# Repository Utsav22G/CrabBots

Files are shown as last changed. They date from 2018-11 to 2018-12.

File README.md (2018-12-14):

# CrabBots
### Small robots that use colored light to interact with other robots and the environment to perform complex interactions. 

## Overview
To learn more about our project, visit our [website!](http://poe.olin.edu/2018/crabworks/)

This github serves a storage capsule for our CAD files, PCB designs, and code used in our project. 

## PCB (Robot)
Our PCB is based off the Arduino Uno and includes some additional features:
* An analog mux for an increased number of anlog input pins
* A dual h-bridge motor driver to power our motors
* A 3-axis accelerometer for tap/bump detection
* Support for an RGB strip. We used NeoPixels

Because our PCB follows the same avr architecture as the Arduino Uno (and uses the same Atmega328P-PB), any Arduino code can be
uploaded through the Arduino IDE compiler to program our boards. However, our boards are lacking usb-serial convertera so an external
usb-serial converter is needed ([this is what we used](https://www.sparkfun.com/products/9825)).

You might notice that our assembled PCBs are populated with only a fraction of the parts that are included in our layout. This is 
due to a radical change in our photodiode sensing circuit after shipping the boards to be manufactured. Fortunately, our new circuit
uses less parts so it's still easy to assemble a working board. 

If you are up for an extra challenge, feel free to submit a pull request for a flashy, new board.

## PCB (Beacon)
What is the best accessory for our CrabBot? A fancy flashlight that can be programmed to display any color and controlled with a
tactile toggle button, of course! Our beacons are a useful tool for debugging and controlling our bots.

The schematic for the board stayed mostly the same. An input for **gnd** and **vcc** are needed for the board to function. We also recommend adding a power switch so the Attiny 85 doesn't drain your battery over time.

## Software
Our final bots rely on two code files: chaser, chased. When uploaded to our CrabBots, this code will make them chase each other. The code is written in Arduino and relys on multiple libraries including the Adafruit sensor library. The appropriate packages that need to be downloaded can be found [here](https://learn.adafruit.com/adafruit-lis3dh-triple-axis-accelerometer-breakout/arduino) and [here](https://learn.adafruit.com/adafruit-neopixel-uberguide/basic-connections). 

## Mechanical Design
The final iteration of CAD can be found here. We printed the components on a Prusa with PLA filament. While this design should not
be constrained by the type of plastic or printer used, we can't guarantee success with another setup. 

## Assembly
While we currently don't have a thorough instruction set layed out, we recommend looking at all our pictures. You probably don't need
or want instructions anyways!

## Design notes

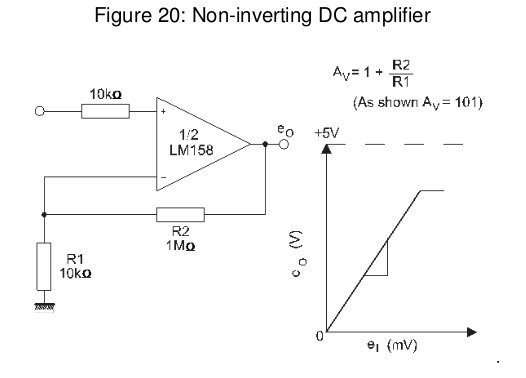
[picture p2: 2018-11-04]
res/lm358_schematic.png

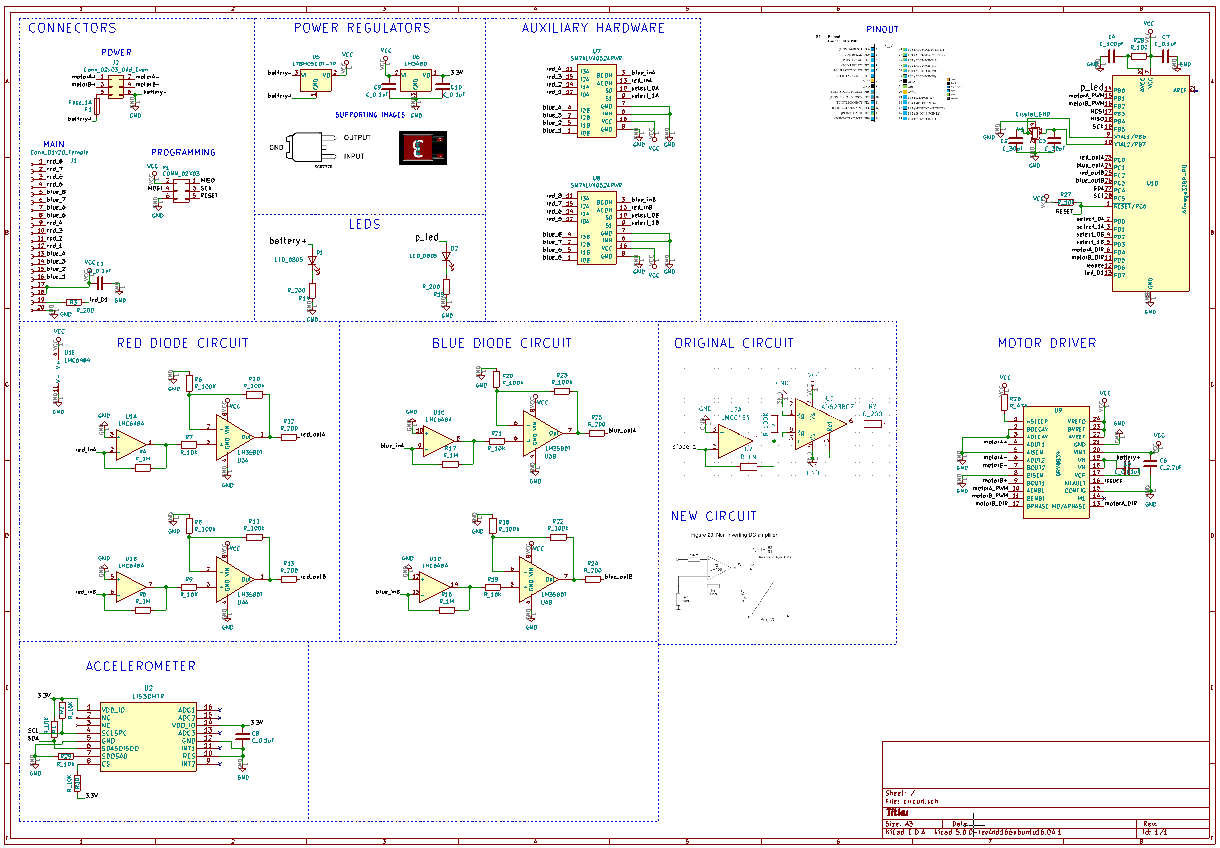
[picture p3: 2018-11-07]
res/circuit_schematic.png

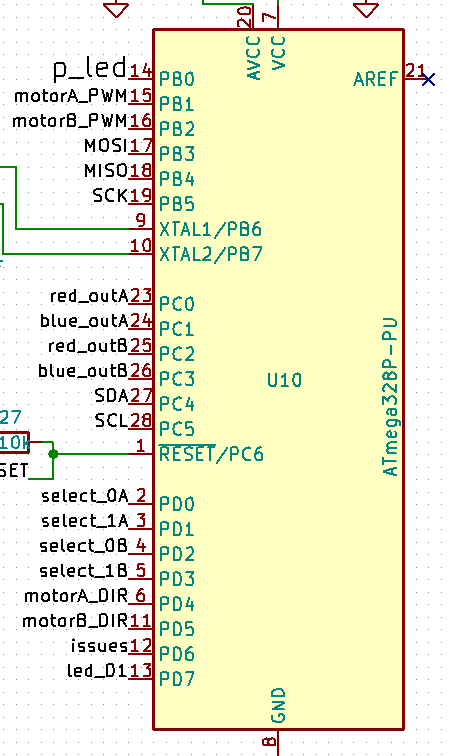
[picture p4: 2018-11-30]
res/atmega_pinout.png

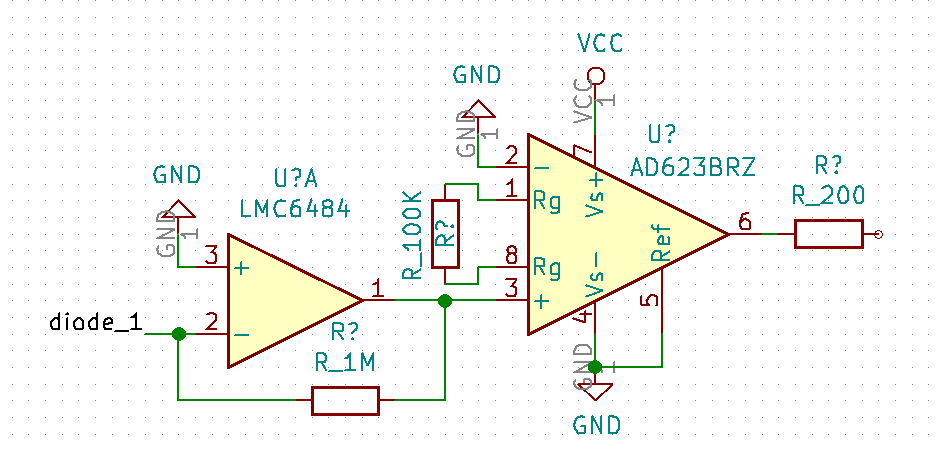
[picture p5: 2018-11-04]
res/original_schematic.png

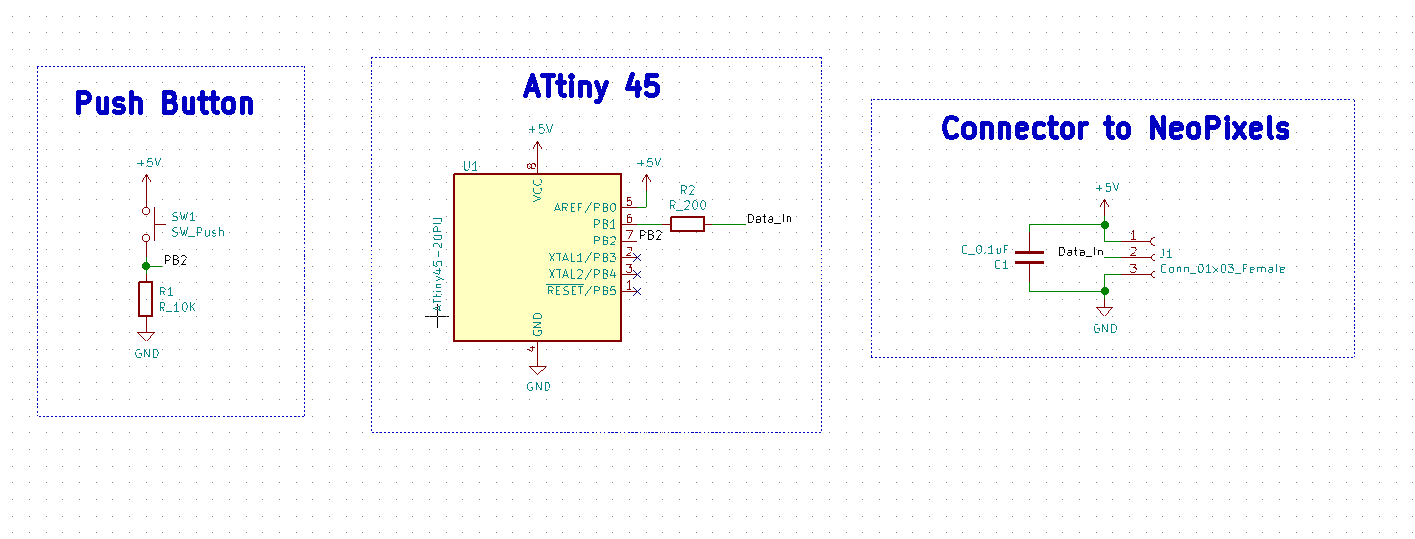
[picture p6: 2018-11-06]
beacon/Schematic.png

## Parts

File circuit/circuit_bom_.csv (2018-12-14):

Component | Description | Part | References | Value | Footprint | Quantity Per PCB | Datasheet | MPN | MFN | PurchasingLink | Package | Purchasing Link
1 | Capacitor, 0.1uF, 50V, 5%, 0805 | C_0.1uF | C5 | C_0.01uF | C_0805_OEM | 1 | http://datasheets.avx.com/X7RDielectric.pdf | 478-3352-1-ND | DK | https://www.digikey.com/product-detail/en/samsung-electro-mechanics/CL21B103KBCSFNC/1276-2439-1-ND/3890525
2 | Capacitor, 0.1uF, 50V, 5%, 0805 | C_0.1uF | C1 C7 C8 C9 C10 | C_0.1uF | C_0805_OEM | 5 | http://datasheets.avx.com/X7RDielectric.pdf | 478-3352-1-ND | DK Digi-Key | https://www.digikey.com/products/en?keywords=478-3352-1-ND | Value
3 | Capacitor, 100pF, 50V, 5%, 0805 | C_100pF | C4 | C_100pF | C_0805_OEM | 1 | https://content.kemet.com/datasheets/KEM_C1003_C0G_SMD.pdf | 399-1122-1-ND | Digi-Key | https://www.digikey.com/product-detail/en/kemet/C0805C101J5GACTU/399-1122-1-ND/411397 | Value
4 | Capacitor, 2.2uF, 10V, 10%, 0603 | C_2.2uF | C6 | C_2.2uF | R_0805_OEM | 1 | http://www.yageo.com/documents/recent/UPY-GPHC_X5R_4V-to-50V_25.pdf | 311-1451-1-ND | DK | https://www.digikey.com/product-detail/en/taiyo-yuden/EMK212BJ225KGHT/587-3323-1-ND/4157368
5 | Capacitor, 30pF, 50V, 5%, 0805 | C_30pF | C2 C3 | C_30pF | C_0805_OEM | 2 | https://media.digikey.com/pdf/Data%20Sheets/Samsung%20PDFs/CL_Series_MLCC_ds.pdf | 1276-1130-1-ND | DK | https://www.digikey.com/product-detail/en/samsung-electro-mechanics-america-inc/CL21C300JBANNNC/1276-1130-1-ND/3889216
6 | LED, Green, 2.2V, 20mA, 0805 | LED_0805 | D1 D2 | LED_0805 | LED_0805_OEM | 2 | http://www.osram-os.com/Graphics/XPic9/00078860_0.pdf | 475-1410-1-ND | DK | https://www.digikey.com/products/en?keywords=475-1410-1-ND
7 | Fuse | Fuse | F1 | Fuse_1A | R_0805_OEM | 1 | https://industrial.panasonic.com/cdbs/www-data/pdf/AFA0000/AFA0000C7.pdf
8 | Generic connector, single row, 01x20, script generated (kicad-library-utils/schlib/autogen/connector/) | Conn_01x20_Female | J1 | Conn_01x20_Female | Pin_Header_Straight_2x10 | 1 | ~
9 | Generic connector, double row, 02x03, odd/even pin numbering scheme (row 1 odd numbers, row 2 even numbers), script generated (kicad-library-utils/schlib/autogen/connector/) | Conn_02x03_Odd_Even | J2 | Conn_02x03_Odd_Even | Pin_Header_Straight_2x03 | 1 | ~
10 |  | CONN_02X03-formula | P1 | CONN_02X03 | Pin_Header_Straight_2x03 | 1 | http://portal.fciconnect.com/Comergent//fci/drawing/67996.pdf | 609-3234-ND | Digi-Key | https://www.digikey.com/product-detail/en/amphenol-fci/67997-206HLF/609-3234-ND/1878491 | Value
11 |  | R_100 | R28 | R_100 | R_0805_OEM | 1 | https://www.seielect.com/Catalog/SEI-rncp.pdf | RNCP0805FTD100RCT-ND | Digi-Key | https://www.digikey.com/products/en?keywords=RNCP0805FTD100RCT-ND | Value
12 |  | R_100K | R6 R8 R10 R11 R18 R20 R22 R23 | R_100K | R_0805_OEM | 8 | https://industrial.panasonic.com/cdbs/www-data/pdf/RDA0000/AOA0000C304.pdf | P100KCCT-ND | DK | https://www.digikey.com/product-detail/en/panasonic-electronic-components/ERJ-6ENF1003V/P100KCCT-ND/119551
13 |  | R_10K | R1 R2 R7 R9 R19 R21 R29 R30 | R_10K | R_0805_OEM | 8 | http://www.bourns.com/data/global/pdfs/CRS.pdf | CRS0805-FX-1002ELFCT-ND | DK | https://www.digikey.com/products/en?keywords=CRS0805-FX-1002ELFCT-ND
14 |  | R_10k-formula | R27 | R_10k | R_0805_OEM | 1 | http://www.bourns.com/data/global/pdfs/CRS.pdf | CRS0805-FX-1002ELFCT-ND | Digi-Key | https://www.digikey.com/products/en?keywords=CRS0805-FX-1002ELFCT-ND | Value
15 |  | R_1M | R4 R5 R16 R17 | R_1M | R_0805_OEM | 4 | https://www.seielect.com/Catalog/SEI-rncp.pdf | RMCF0805JT1M00CT-ND | DK | https://www.digikey.com/product-detail/en/stackpole-electronics-inc/RMCF0805JT1M00/RMCF0805JT1M00CT-ND/1942600
16 |  | R_200 | R3 R12 R13 R14 R15 R24 R25 | R_200 | R_0805_OEM | 7 | https://www.seielect.com/Catalog/SEI-RMCF_RMCP.pdf | RMCF0805JT200RCT-ND | DK | https://www.digikey.com/products/en?keywords=RMCF0805JT200RCT-ND
17 |  | R_1K | R26 | R_47K | R_0805_OEM | 1 | https://www.seielect.com/Catalog/SEI-rncp.pdf | RNCP0805FTD1K00CT-ND | DK | https://www.digikey.com/products/en?keywords=RNCP0805FTD1K00CT-ND
18 |  | ATmega328P-PU-MCU_Microchip_ATmega | U10 | ATmega328P-PU | ATMEGA_328PB_CONN | 1 | http://ww1.microchip.com/downloads/en/DeviceDoc/ATmega328_P%20AVR%20MCU%20with%20picoPower%20Technology%20Data%20Sheet%2040001984A.pdf
19 |  | DRV8834-formula | U9 | DRV8834 | DRV8834PWP | 1 | www.ti.com/lit/ds/symlink/drv8834.pdf |  |  |  |  | https://www.digikey.com/product-detail/en/texas-instruments/DRV8834PWP/296-30428-5-ND/3088200
20 | 1A Low Dropout regulator, positive, 5.0V fixed output, SOT-223 | AMS1117-5.0 | U5 | L78M05CDT-TR | L78M05CDT-TR | 1 | www.st.com/content/ccc/resource/technical/document/datasheet/d7/5f/dc/5c/d5/b6/48/7c/CD00000447.pdf/files/CD00000447.pdf/jcr:content/translations/en.CD0000044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
21 |  | LIS3DHTR-formula | U2 | LIS3DHTR | LIS3DHTR | 1
22 | Linear regulator, 30V max input, 3.3V output, 100mA | LM3480 | U6 | LM3480 | SOT-23 | 1 | http://www.ti.com/lit/ds/symlink/lm3480.pdf | LM3480IM3-3.3CT-ND | DK | https://www.digikey.com/product-detail/en/texas-instruments/LM3480IM3-3.3/LM3480IM3-3.3CT-ND/3701583
23 |  | LM358DT-formula | U3 U4 | LM358DT | SO-8_5.3x6.2mm_Pitch1.27mm | 2 | www.st.com/content/ccc/resource/technical/document/datasheet/61/46/87/01/98/ed/44/c5/CD00000464.pdf/files/CD00000464.pdf/jcr:content/translations/en.CD0000046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 |  |  | https://www.digikey.com/product-detail/en/stmicroelectronics/LM358DT/497-1591-1-ND/592083
24 | Quad CMOS Rail-to-Rail Input and Output Operational Amplifier, DIP-14/SOIC-14 | LMC6484 | U1 | LMC6484 | SOIC-14_3.9x8.7mm_Pitch1.27mm | 1 | http://www.ti.com/lit/ds/symlink/lmc6484.pdf
25 |  | SN74LV4052APWR-formula | U7 U8 | SN74LV4052APWR | TSSOP-16_4.4x5mm_Pitch0.65mm | 2 | www.ti.com/lit/ds/symlink/sn74lv4052a.pdf |  |  |  |  | https://www.digikey.com/product-detail/en/texas-instruments/SN74LV4052APWR/296-3831-1-ND/390425
26 | CRYSTAL 16.0000MHZ 18PF SMD | Crystal_SMD | Y1 | Crystal_SMD | Crystal_SMD_FA238 | 1 | http://www.txccorp.com/download/products/quartz_crystals/2015TXC_7M_17.pdf | 887-1125-1-ND | DK | https://www.digikey.com/product-detail/en/txc-corporation/7M-16.000MAAJ-T/887-1125-1-ND/2119014
Component Groups: | 26
Component Count: | 57
Fitted Components: | 57
Number of PCBs: | 1
Total components: | 57
Schematic Version:
Schematic Date:
BoM Date: | Wed 21 Nov 2018 11:47:25 PM EST
Schematic Source: | /home/utsav22g/Olin Stuff/CrabBots/circuit/circuit.sch
KiCad Version: | Eeschema 5.0.1-33cea8e~68~ubuntu18.04.1

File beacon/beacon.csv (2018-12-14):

Id | Designator | Package | Quantity | Designation | Supplier and ref
1 | C1 | C_0805_OEM | 1 | C_0.1uF
2 | J1 | Connector | 1 | Conn_01x03_Female
3 | R1 | R_0805_OEM | 1 | R_10K
4 | R2 | R_0805_OEM | 1 | R_200
5 | SW1 | push_button | 1 | SW_Push
6 | U1 | DIP-8_W7.62mm_Socket | 1 | ATtiny45-20PU

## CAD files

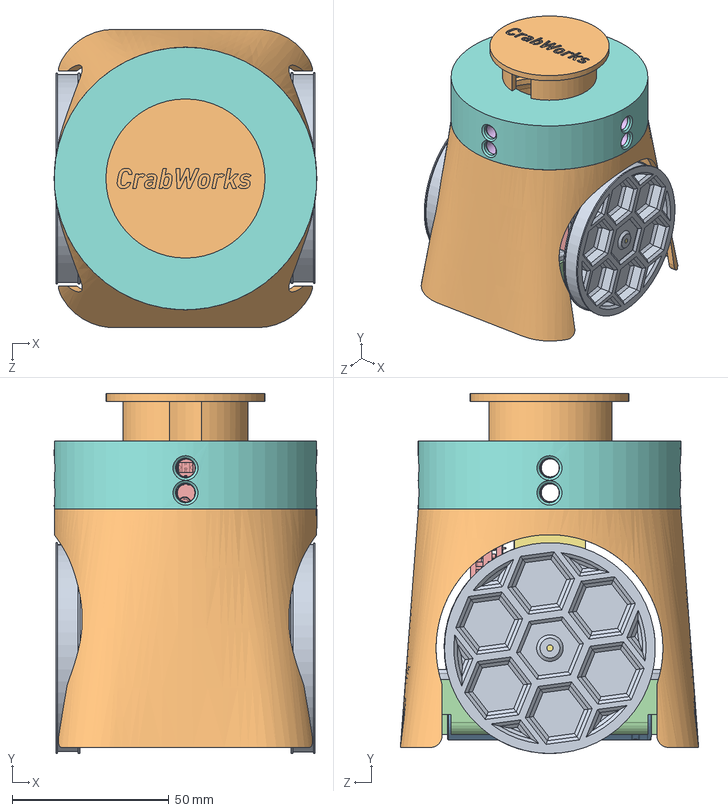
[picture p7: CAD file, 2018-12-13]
CrabBot_CAD/Assem_v5.SLDASM
83.8 x 114.9 x 95.2 mm
Chassis_v5
Shell_v5
2_cell_holder_18650_v5
arduino uno
DovetailLightSensor_v5 x 4
Pololu Mini Plastic Gearmotor x 2
Top_v5
wheel_v5 x 2
Beacon_Top_Bot_v5

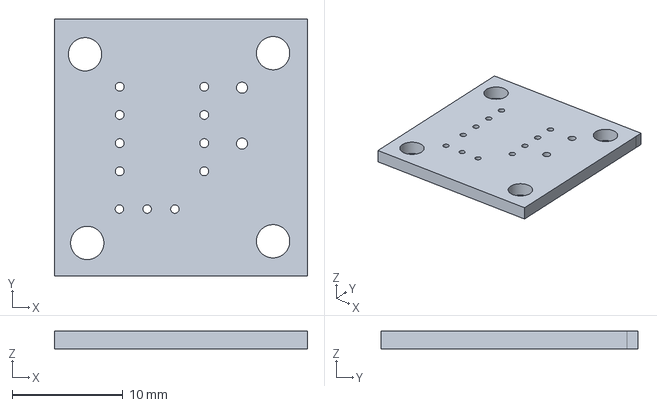
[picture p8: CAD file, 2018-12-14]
beacon/beacon.step
22.8 x 23.2 x 1.60 mm

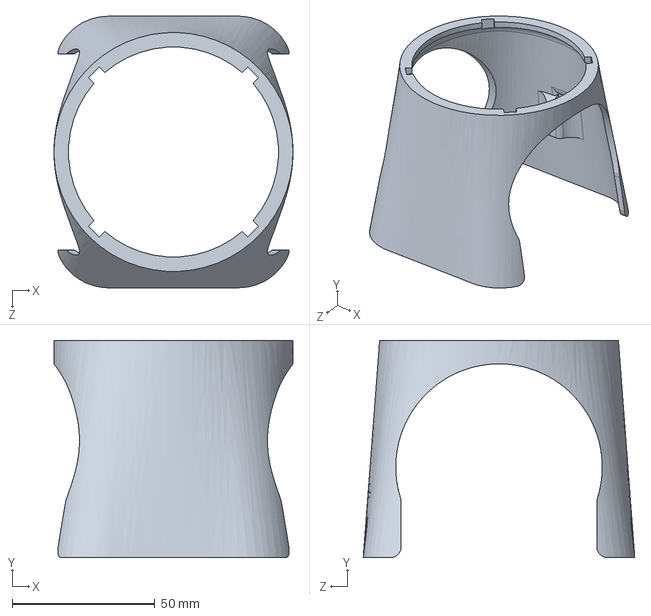
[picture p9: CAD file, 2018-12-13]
CrabBot_CAD/Shell_v5.SLDPRT
83.8 x 76.2 x 95.2 mm

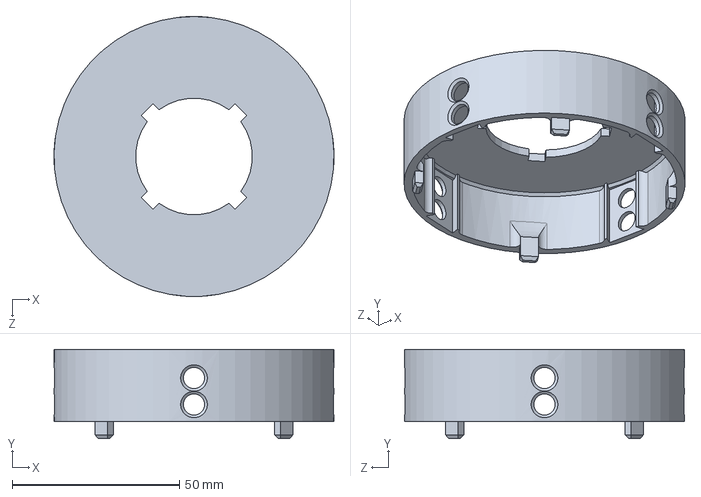
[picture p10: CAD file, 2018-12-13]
CrabBot_CAD/Top_v5.SLDPRT
83.8 x 26.7 x 83.8 mm

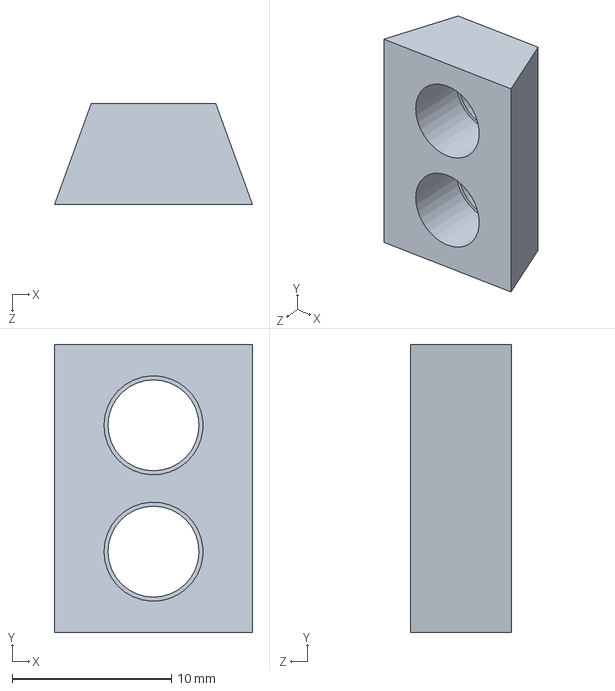
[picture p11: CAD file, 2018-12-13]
CrabBot_CAD/DovetailLightSensor_v5.SLDPRT
12.4 x 18.1 x 6.35 mm

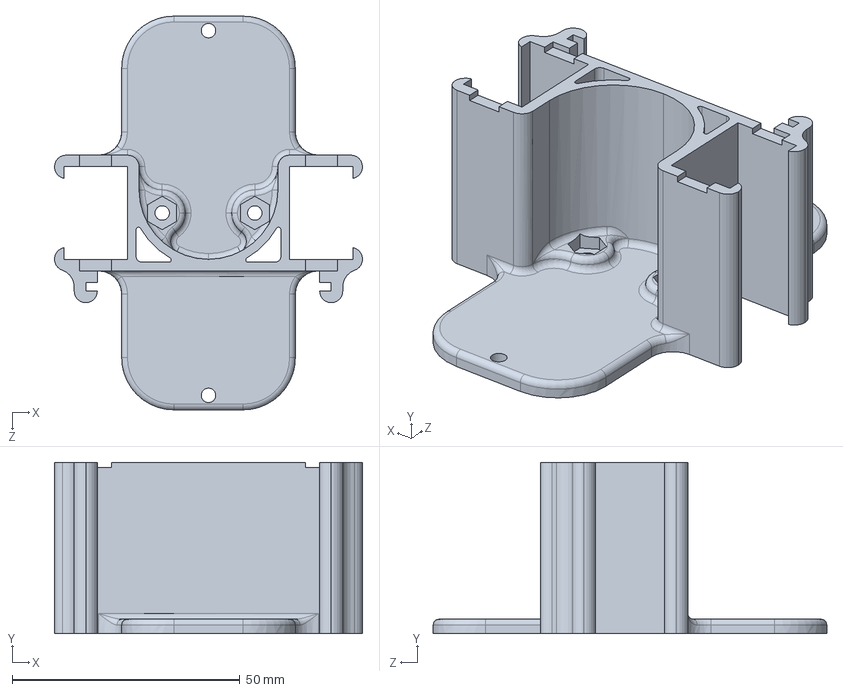
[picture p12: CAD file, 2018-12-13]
CrabBot_CAD/Chassis_v5.SLDPRT
67.6 x 37.6 x 86.4 mm

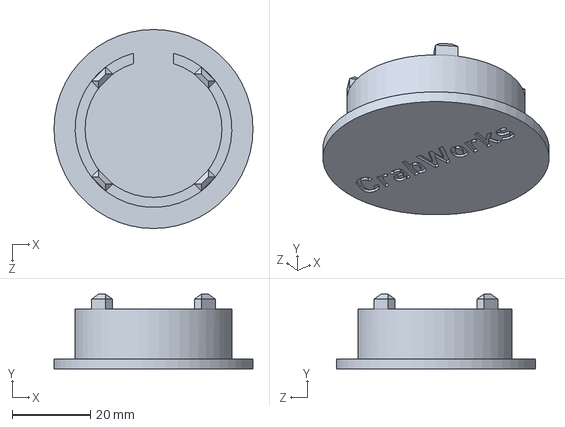
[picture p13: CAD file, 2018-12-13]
CrabBot_CAD/Beacon_Top_Bot_v5.SLDPRT
50.8 x 19.1 x 50.8 mm

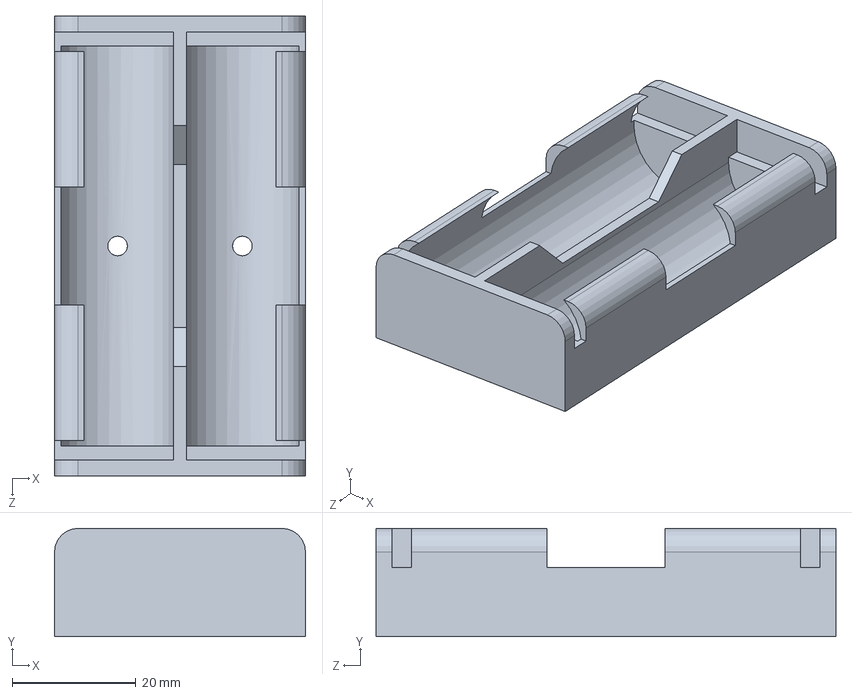
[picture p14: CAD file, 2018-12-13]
CrabBot_CAD/2_cell_holder_18650_v5.SLDPRT
40.6 x 17.5 x 74.4 mm

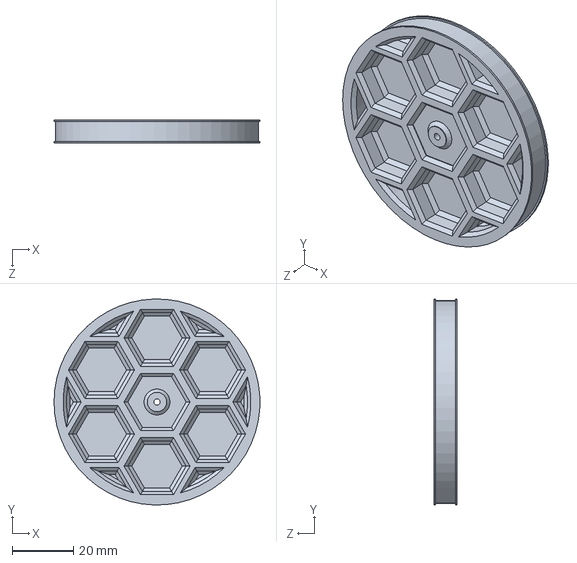
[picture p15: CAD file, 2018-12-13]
CrabBot_CAD/wheel_v5.SLDPRT
67.3 x 67.3 x 7.62 mm

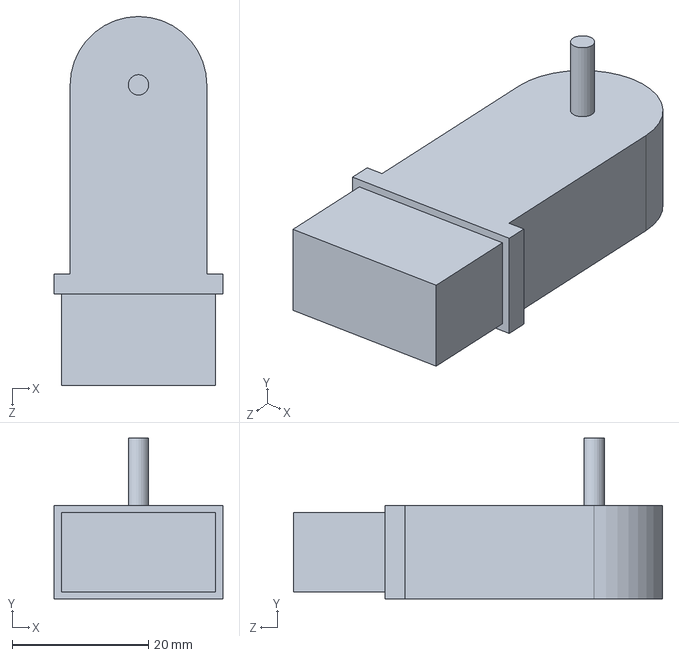
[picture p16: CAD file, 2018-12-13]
CrabBot_CAD/Pololu Mini Plastic Gearmotor.SLDPRT
24.7 x 23.6 x 54.1 mm

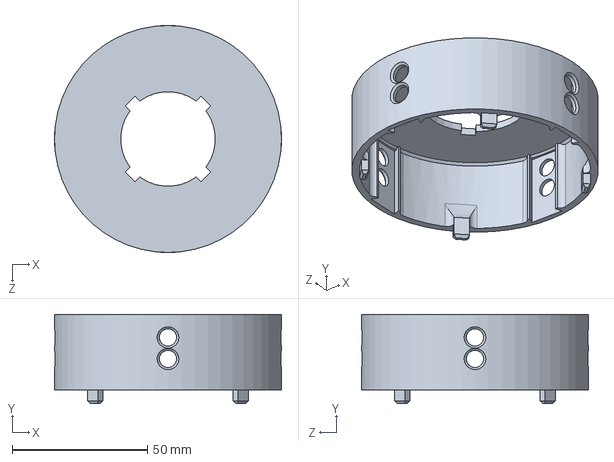
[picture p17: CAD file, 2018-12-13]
CrabBot_CAD/Top_v5_extended.SLDPRT
83.8 x 33.0 x 83.8 mm

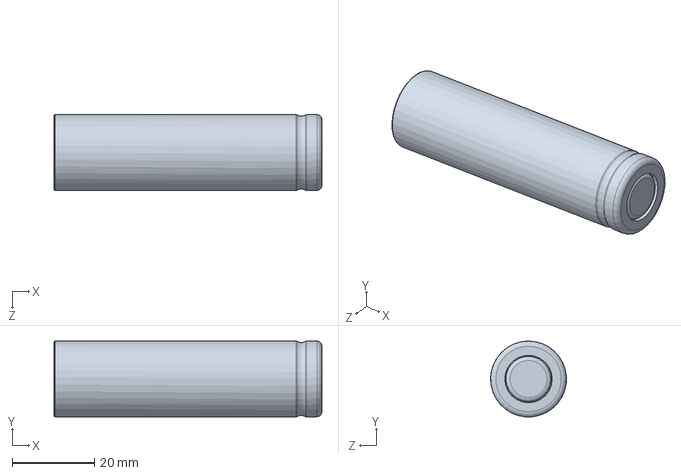
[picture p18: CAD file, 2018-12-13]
CrabBot_CAD/18650.SLDPRT
65.0 x 18.4 x 18.4 mm

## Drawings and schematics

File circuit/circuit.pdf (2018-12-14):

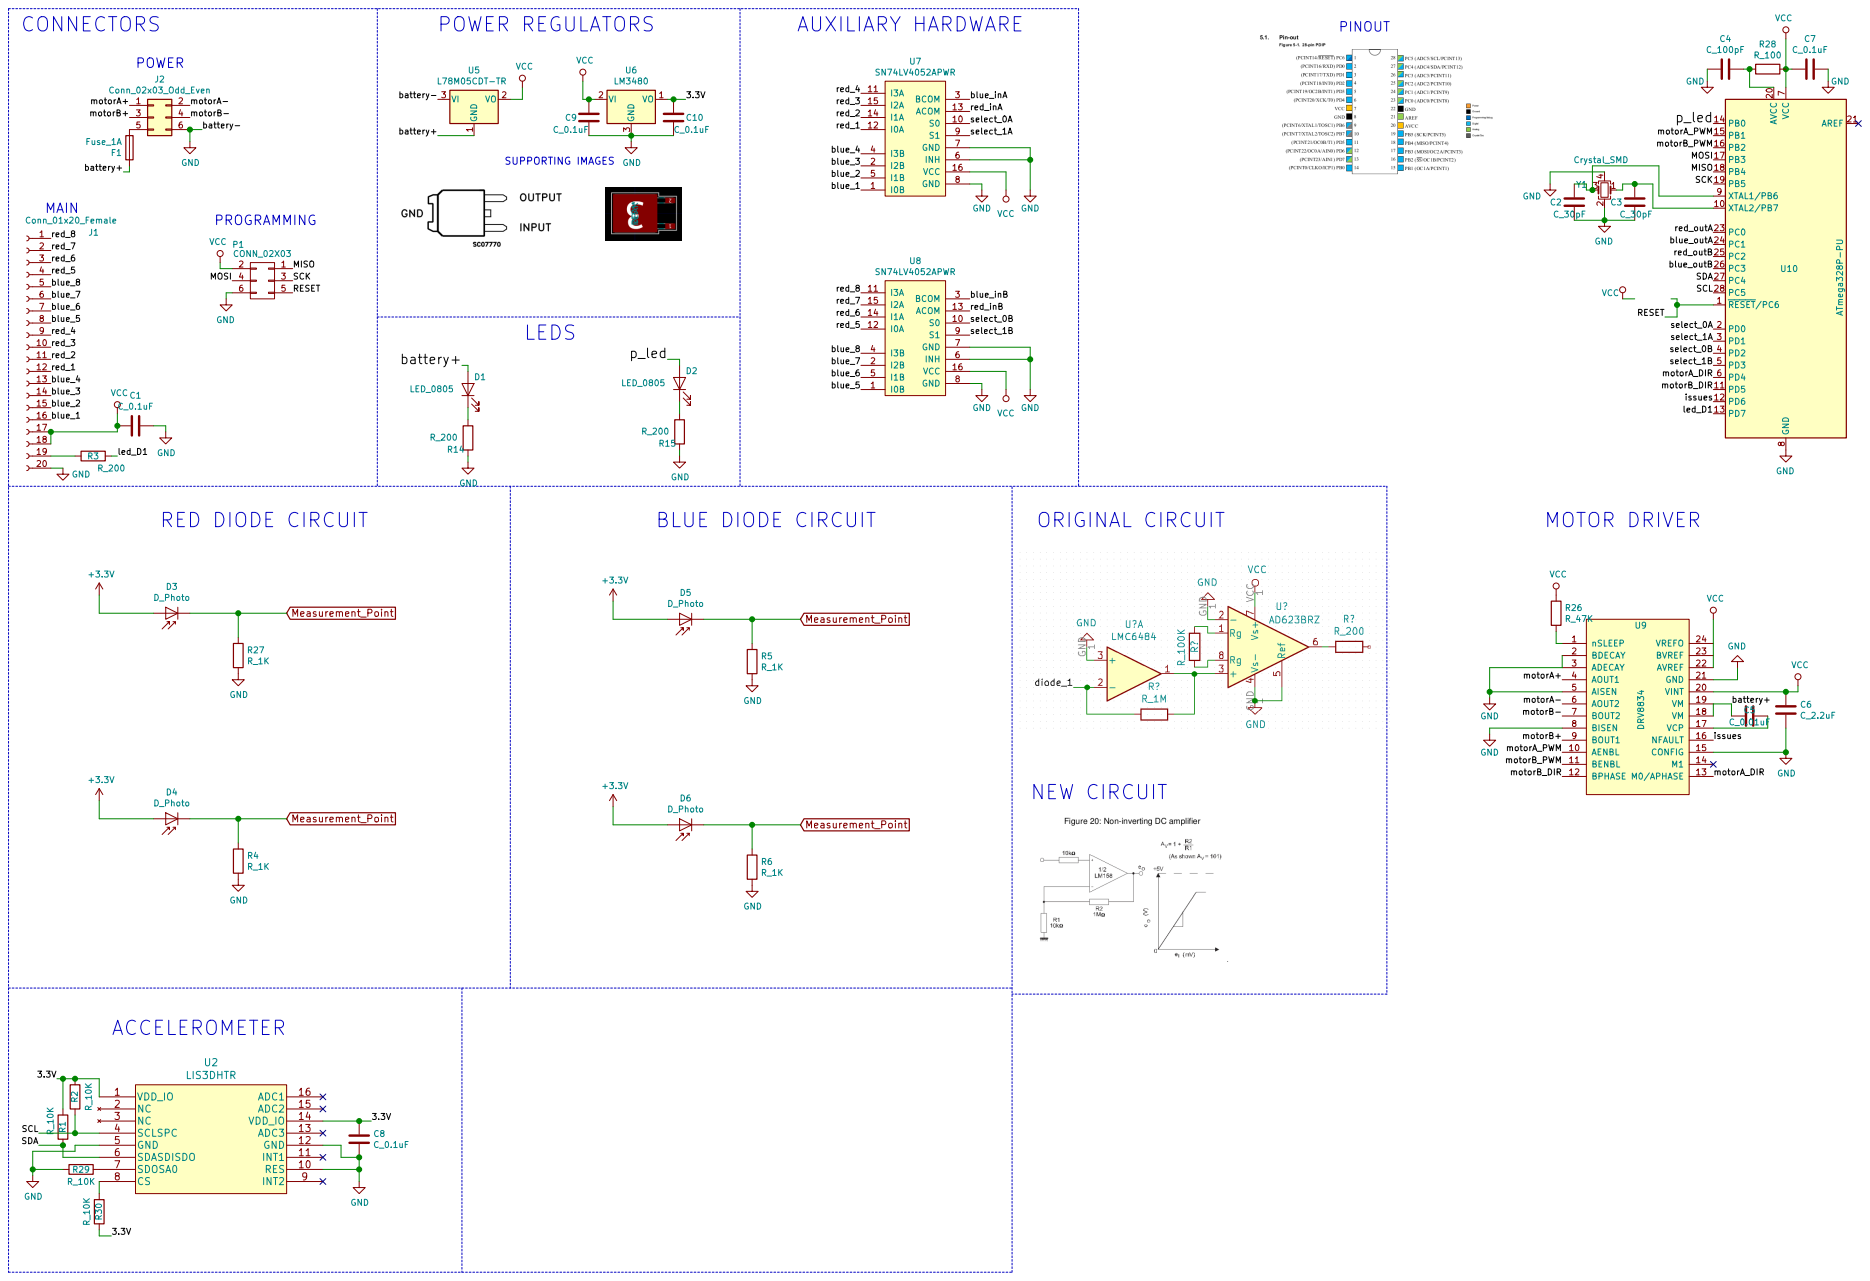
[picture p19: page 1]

LED_0805R15 R_200 GND SUPPORTING IMAGES LEDS

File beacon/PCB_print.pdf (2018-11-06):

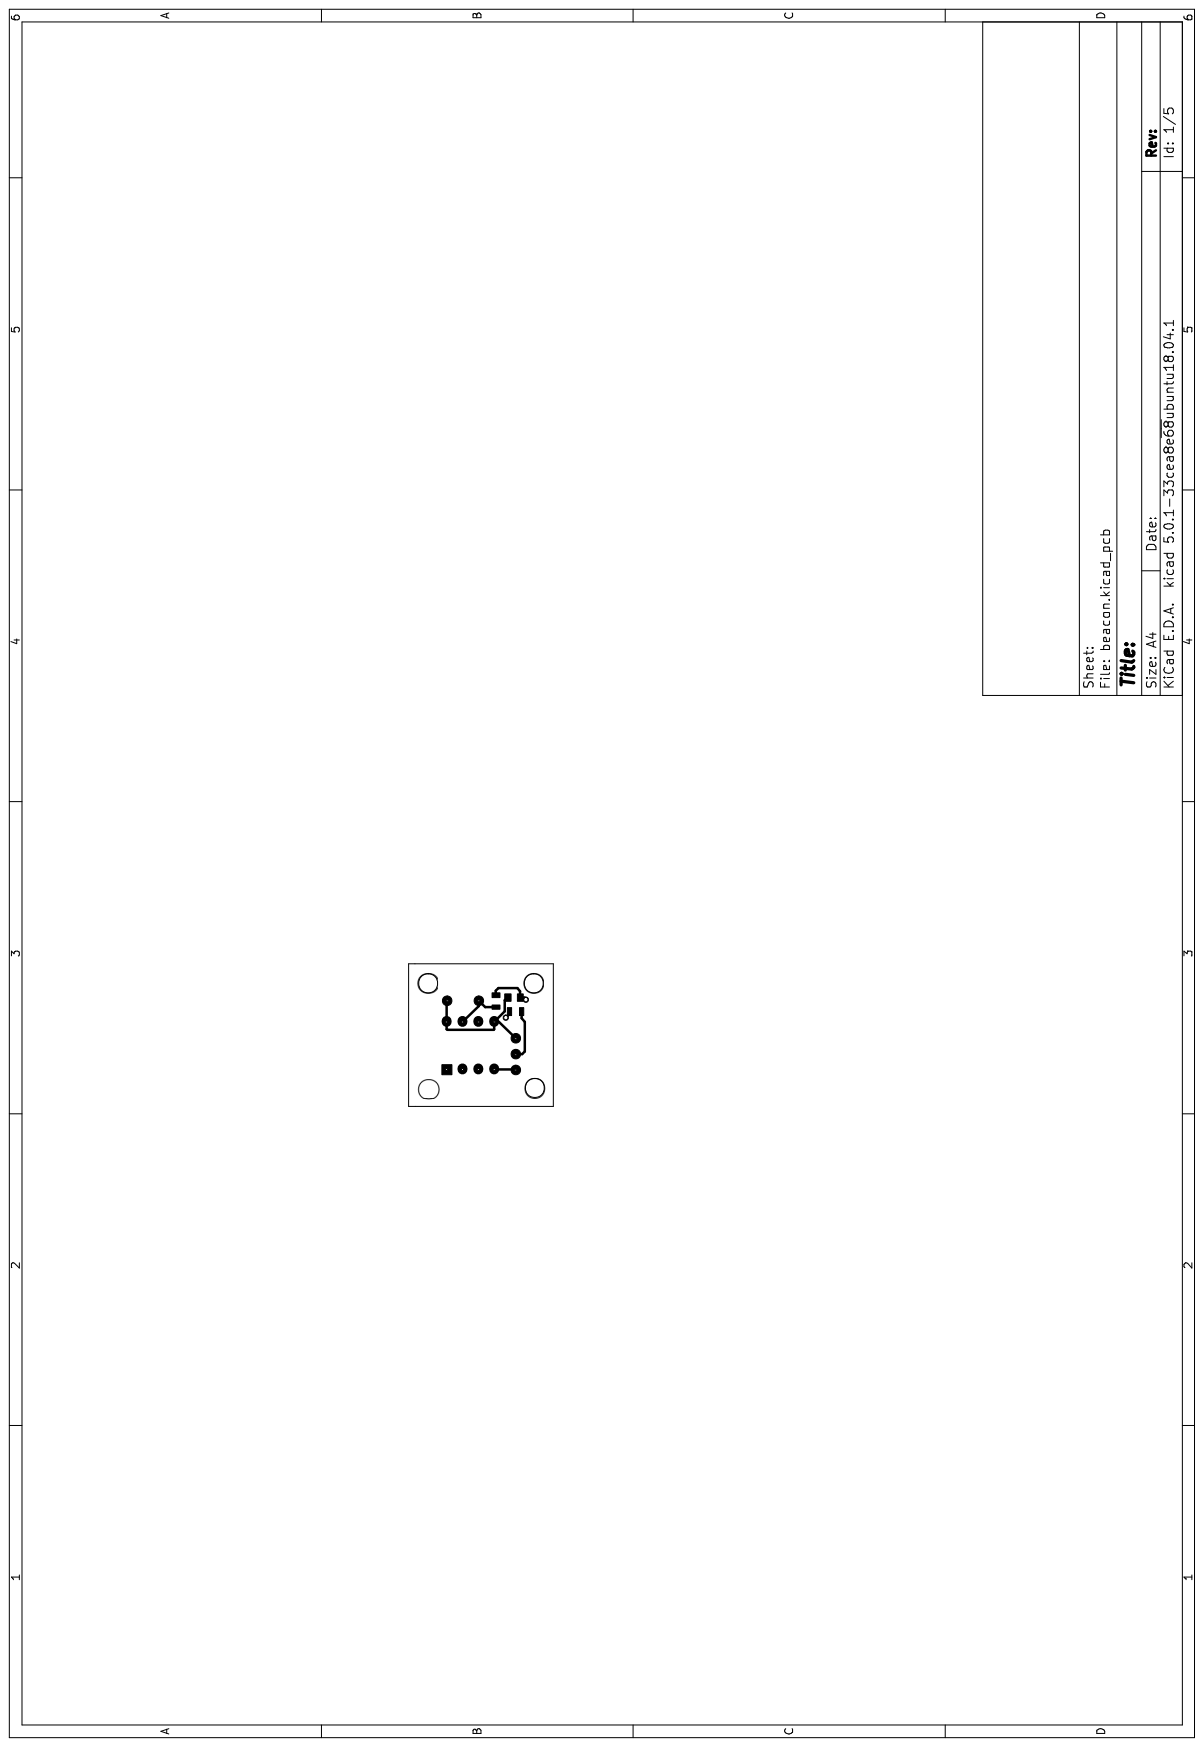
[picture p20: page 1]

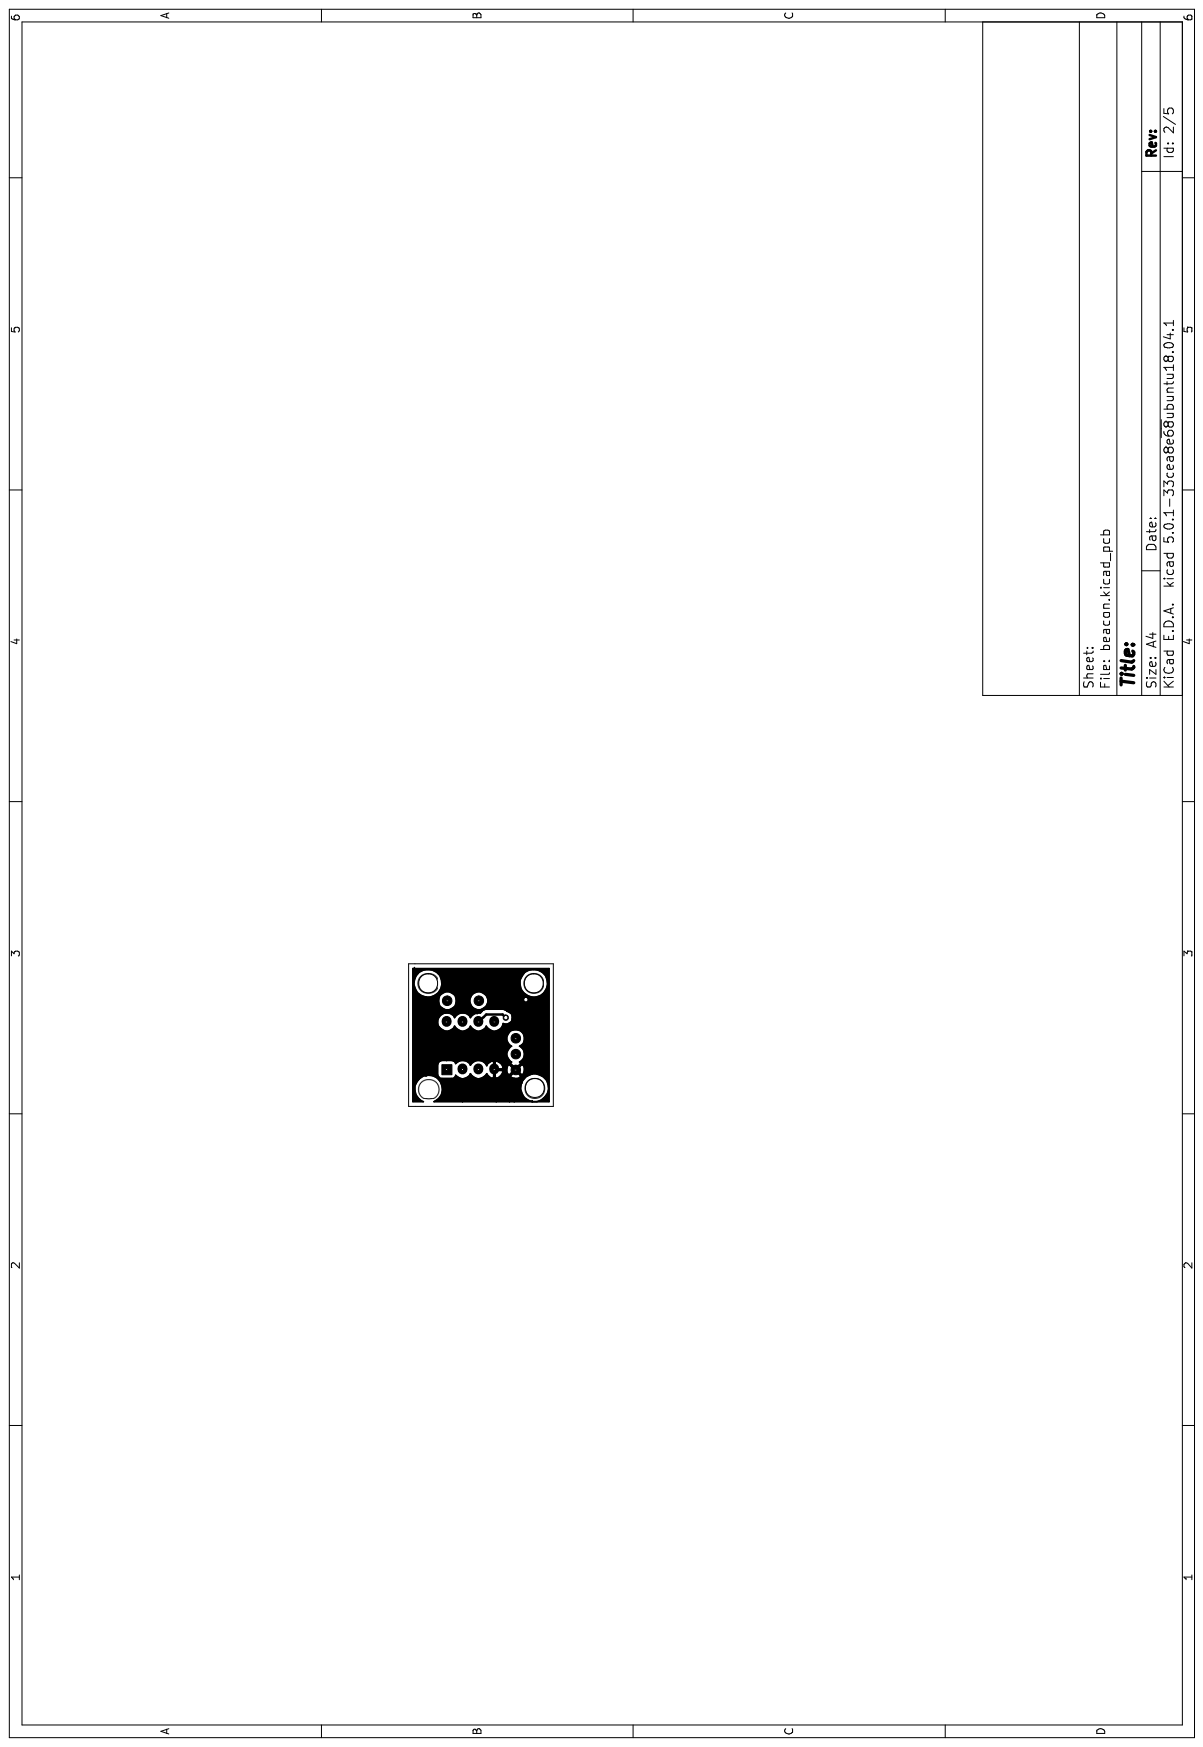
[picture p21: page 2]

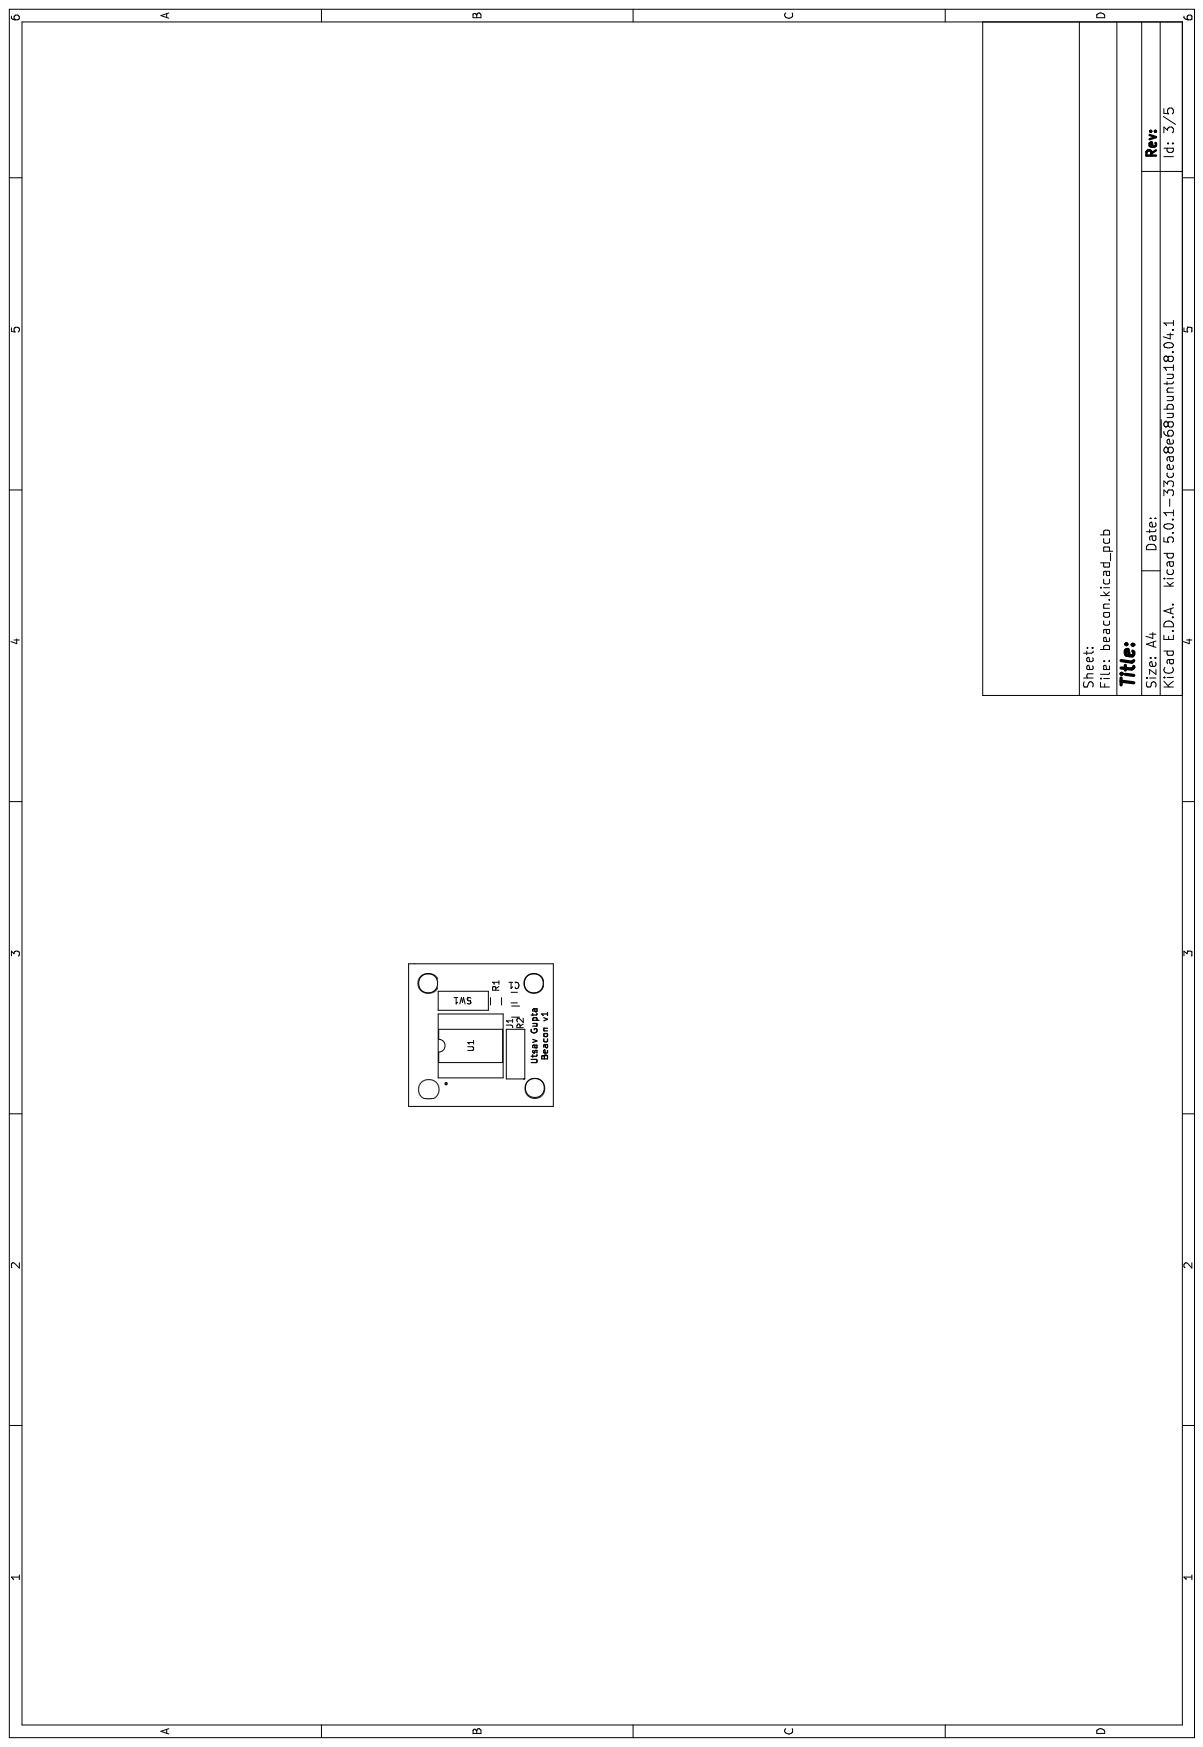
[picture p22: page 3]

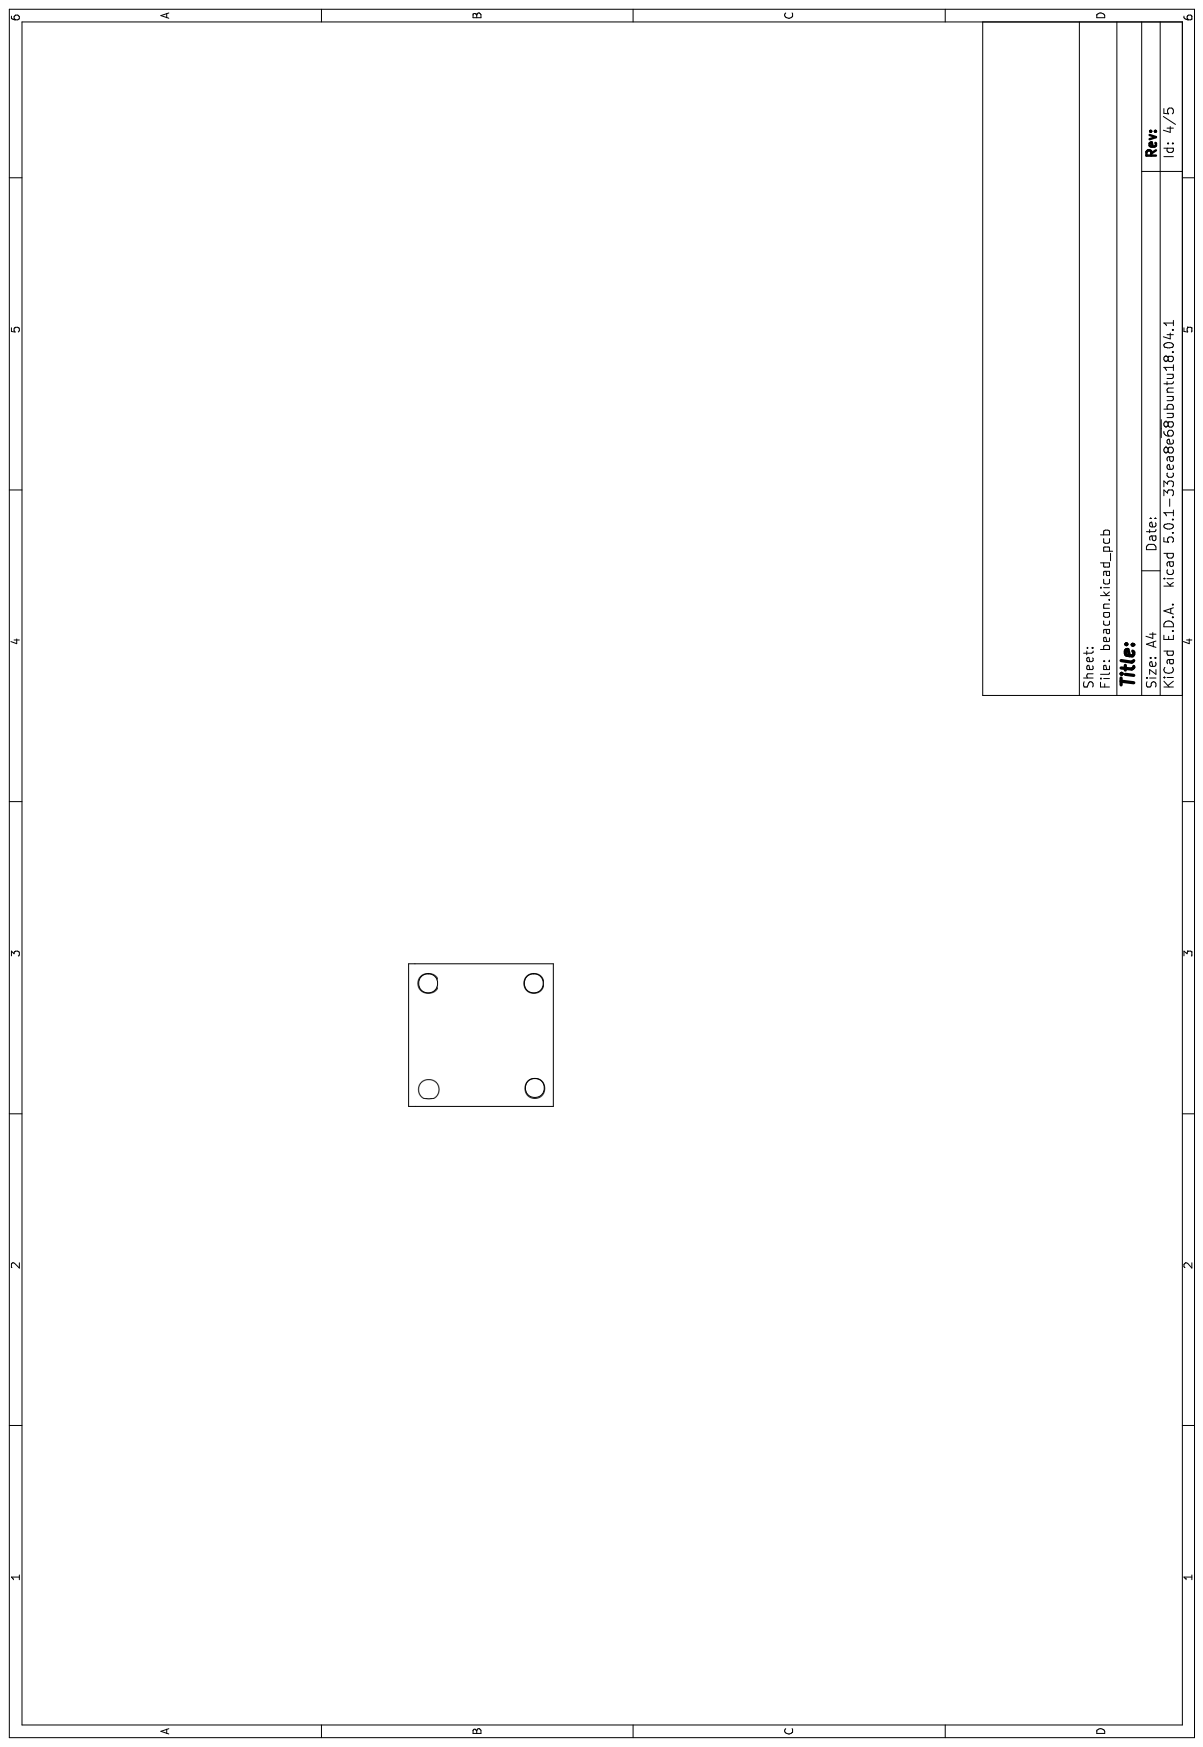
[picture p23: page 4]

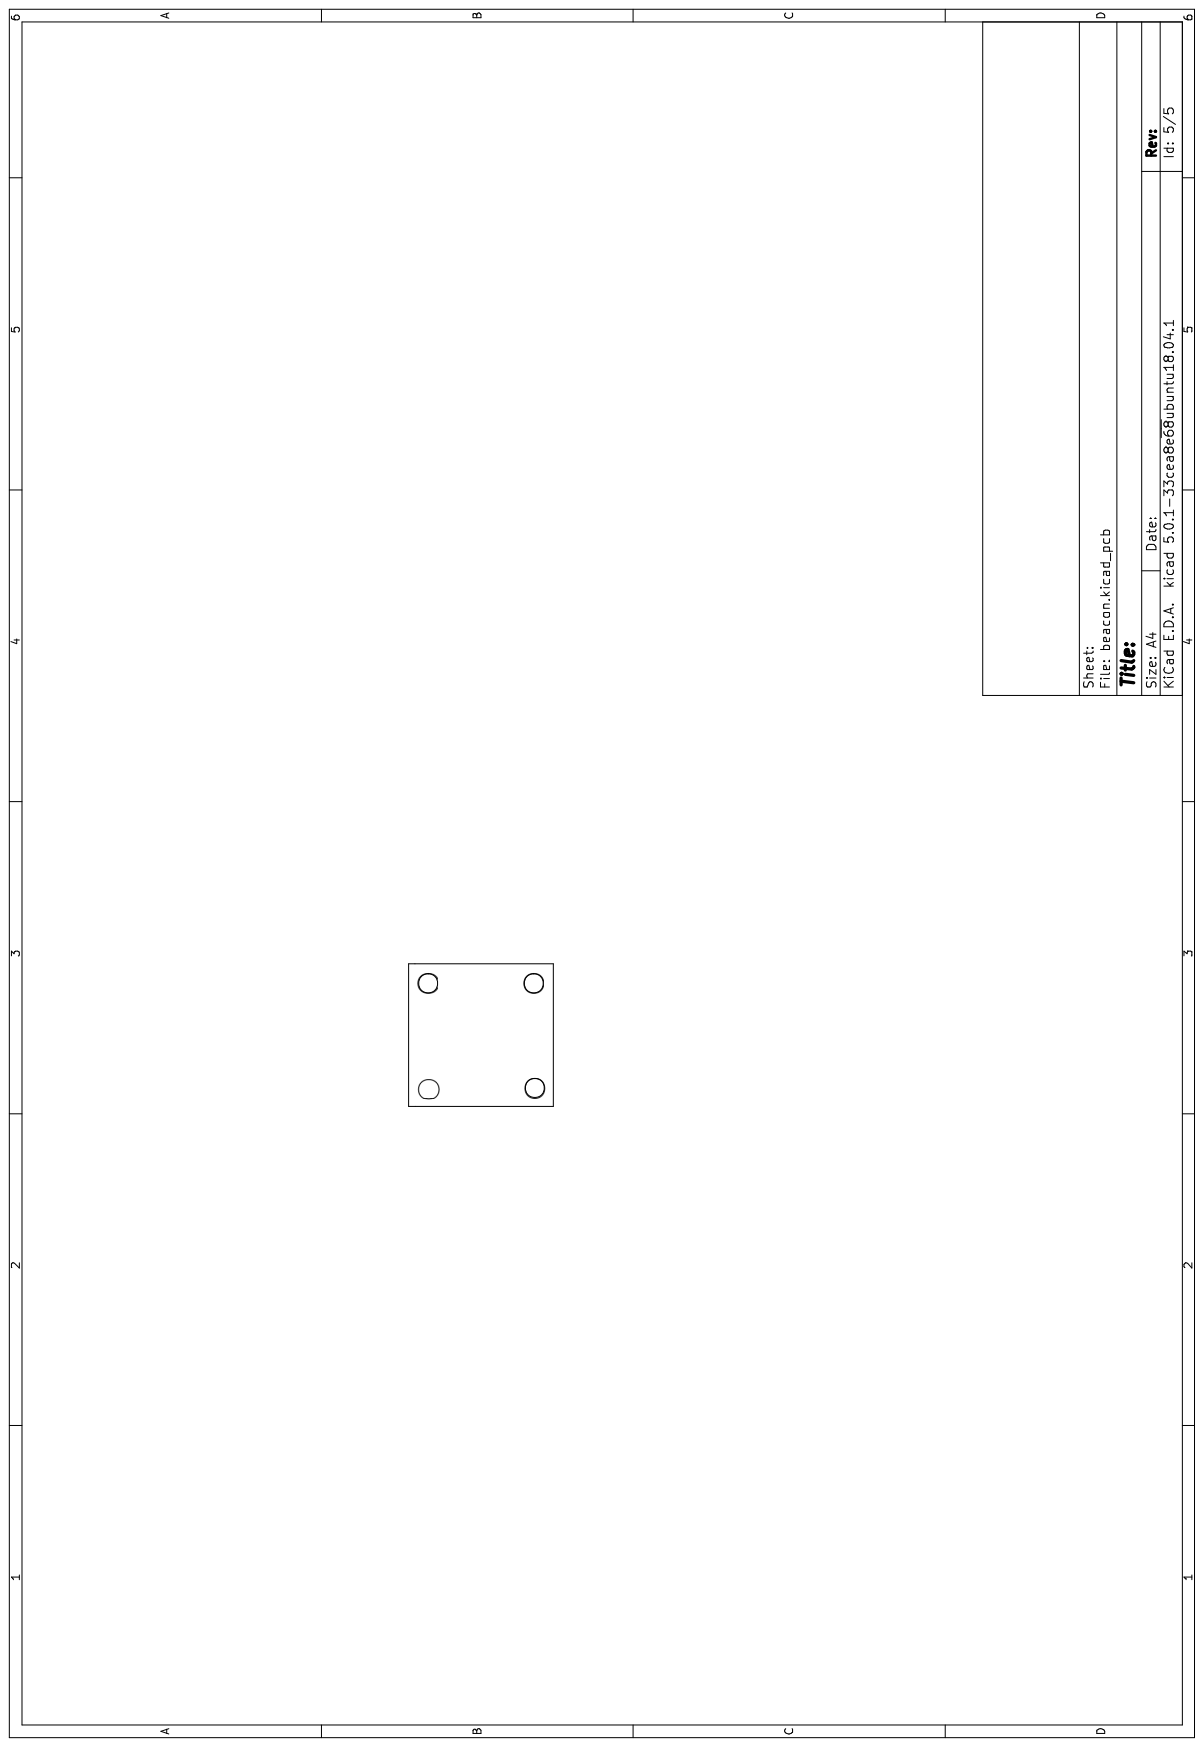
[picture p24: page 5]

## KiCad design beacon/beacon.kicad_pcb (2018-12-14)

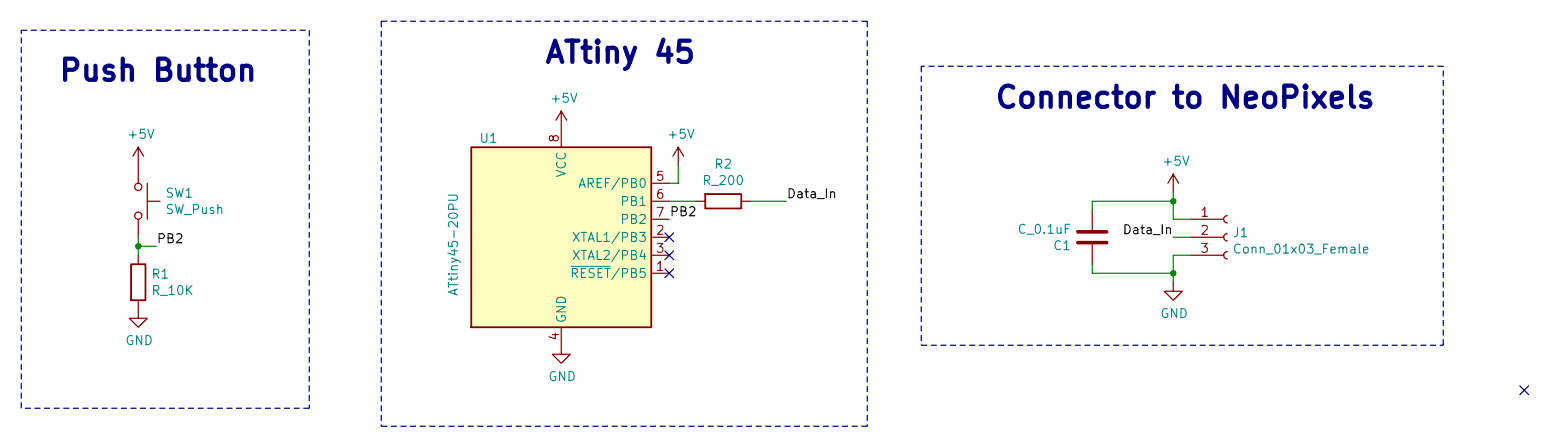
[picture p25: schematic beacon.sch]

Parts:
C1: C_0.1uF; C_0805_OEM; MPN 478-3352-1-ND
J1: Conn_01x03_Female; Connector
R1: R_10K; R_0805_OEM; MPN CRS0805-FX-1002ELFCT-ND
R2: R_200; R_0805_OEM; MPN RMCF0805JT200RCT-ND
SW1: SW_Push; push_button
U1: ATtiny45-20PU; DIP-8_W7.62mm_Socket

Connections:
+5V: C1.2, J1.1, SW1.1, U1.5 (AREF/PB0), U1.8 (VCC)
/Data_In: J1.2, R2.1
/PB2: R1.1, SW1.2, U1.7 (PB2)
GND: C1.1, J1.3, R1.2, U1.4 (GND)
unnamed: R2.2, U1.6 (PB1)

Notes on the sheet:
ATtiny 45
Connector to NeoPixels
Push Button

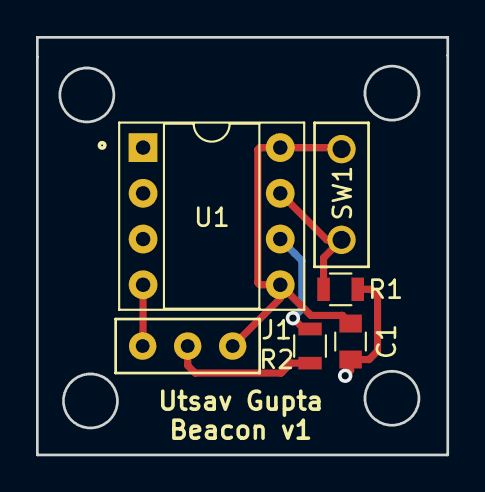
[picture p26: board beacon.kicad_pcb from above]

Board: 2 copper layers, 22.8 x 23.2 mm, 6 parts (0 on the bottom side), 5 nets.

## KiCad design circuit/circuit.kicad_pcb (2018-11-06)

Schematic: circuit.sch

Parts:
C1, C7, C8, C9, C10: C_0.1uF; C_0805_OEM; MPN 478-3352-1-ND
C2, C3: C_30pF; C_0805_OEM; MPN 1276-1130-1-ND
C4: C_100pF; C_0805_OEM; MPN 399-1122-1-ND
C5: C_0.01uF; C_0805_OEM; MPN 478-3352-1-ND
C6: C_2.2uF; R_0805_OEM; MPN 311-1451-1-ND
D1, D2: LED_0805; LED_0805_OEM; MPN 475-1410-1-ND
F1: Fuse_1A; R_0805_OEM
J1: Conn_01x20_Female; Pin_Header_Straight_2x10
J2: Conn_02x03_Odd_Even; Pin_Header_Straight_2x03
P1: CONN_02X03; Pin_Header_Straight_2x03; MPN 609-3234-ND
R1, R2, R7, R9, R19, R21, R29, R30: R_10K; R_0805_OEM; MPN CRS0805-FX-1002ELFCT-ND
R3, R12, R13, R14, R15, R24, R25: R_200; R_0805_OEM; MPN RMCF0805JT200RCT-ND
R4, R5, R16, R17: R_1M; R_0805_OEM; MPN RMCF0805JT1M00CT-ND
R6, R8, R10, R11, R18, R20, R22, R23: R_100K; R_0805_OEM; MPN P100KCCT-ND
R26: R_47K; R_0805_OEM; MPN RNCP0805FTD1K00CT-ND
R27: R_10k; R_0805_OEM; MPN CRS0805-FX-1002ELFCT-ND
R28: R_100; R_0805_OEM; MPN RNCP0805FTD100RCT-ND
U1: LMC6484; SOIC-14_3.9x8.7mm_Pitch1.27mm
U2: LIS3DHTR
U3, U4: LM358DT; SO-8_5.3x6.2mm_Pitch1.27mm
U5: L78M05CDT-TR
U6: LM3480; SOT-23; MPN LM3480IM3-3.3CT-ND
U7, U8: SN74LV4052APWR; TSSOP-16_4.4x5mm_Pitch0.65mm
U9: DRV8834; DRV8834PWP
U10: ATmega328P-PU; ATMEGA_328PB_CONN
Y1: Crystal_SMD; Crystal_SMD_FA238; MPN 887-1125-1-ND

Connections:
/3.3V: C8.1, C10.1, R1.2, R2.2, R30.1, U2.1, U2.14, U6.1
/MISO: P1.1, U10.18 (PB4)
/MOSI: P1.4, U10.17 (PB3)
/RESET: P1.5, R27.2, U10.1 (~RESET~/PC6)
/SCK: P1.3, U10.19 (PB5)
/SCL: R2.1, U2.4, U10.28 (PC5)
/SDA: R1.1, U2.6, U10.27 (PC4)
/battery+: C5.2, D1.2, F1.1, U5.1 (GND), U9.18, U9.19
/blue_1: J1.16, U7.1
/blue_2: J1.15, U7.5
/blue_3: J1.14, U7.2
/blue_4: J1.13, U7.4
/blue_5: J1.8, U8.1
/blue_6: J1.7, U8.5
/blue_7: J1.6, U8.2
/blue_8: J1.5, U8.4
/blue_inA: R17.2, U1.9 (-), U7.3
/blue_inB: R16.2, U1.13 (-), U8.3
/blue_outA: R25.1, U10.24 (PC1)
/blue_outB: R24.1, U10.26 (PC3)
/issues: U9.16, U10.12 (PD6)
/led_D1: R3.1, U10.13 (PD7)
/motorA+: J2.1, U9.4
/motorA-: J2.2, U9.6
/motorA_DIR: U9.13, U10.6 (PD4)
/motorA_PWM: U9.10, U10.15 (PB1)
/motorB+: J2.3, U9.9
/motorB-: J2.4, U9.7
/motorB_DIR: U9.12, U10.11 (PD5)
/motorB_PWM: U9.11, U10.16 (PB2)
/p_led: D2.2, U10.14 (PB0)
/red_1: J1.12, U7.12
/red_2: J1.11, U7.14
/red_3: J1.10, U7.15
/red_4: J1.9, U7.11
/red_5: J1.4, U8.12
/red_6: J1.3, U8.14
/red_7: J1.2, U8.15
/red_8: J1.1, U8.11
/red_inA: R4.2, U1.2 (-), U7.13
/red_inB: R5.2, U1.6 (-), U8.13
/red_outA: R12.1, U10.23 (PC0)
/red_outB: R13.1, U10.25 (PC2)
/select_0A: U7.10, U10.2 (PD0)
/select_0B: U8.10, U10.4 (PD2)
/select_1A: U7.9, U10.3 (PD1)
/select_1B: U8.9, U10.5 (PD3)
unnamed: C2.1, U10.9 (XTAL1/PB6), Y1.3
unnamed: C3.1, U10.10 (XTAL2/PB7), Y1.1
unnamed: C4.2, R28.1, U10.20 (AVCC)
unnamed: C5.1, U9.17
unnamed: D1.1, R14.2
unnamed: D2.1, R15.2
unnamed: F1.2, J2.5
unnamed: J1.19, R3.2
unnamed: R4.1, R7.2, U1.1
unnamed: R5.1, R9.2, U1.7
unnamed: R7.1, U3.3
unnamed: R9.1, U4.3
unnamed: R10.1, R12.2, U3.1
unnamed: R6.2, R10.2, U3.2
unnamed: R11.1, R13.2, U4.1
unnamed: R8.2, R11.2, U4.2
unnamed: R16.1, R19.2, U1.14
unnamed: R17.1, R21.2, U1.8
unnamed: R18.2, R22.2, U4.6
unnamed: R19.1, U4.5
unnamed: R20.2, R23.2, U3.6
unnamed: R21.1, U3.5
unnamed: R22.1, R24.2, U4.7
unnamed: R23.1, R25.2, U3.7
unnamed: R26.2, U9.1
unnamed: R29.1, U2.7
unnamed: R30.2, U2.8
VCC: C1.2, C6.1, C7.1, C9.1, J1.17, J1.18, P1.2, R26.1, R27.1, R28.2, U1.4 (V+), U3.8, U4.8, U5.2 (VO), U6.2, U7.16, U8.16, U9.20, U9.22, U9.23, U9.24, U10.7 (VCC)

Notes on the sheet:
RED DIODE CIRCUIT
BLUE DIODE CIRCUIT
ORIGINAL CIRCUIT
NEW CIRCUIT
CONNECTORS
MOTOR DRIVER
POWER REGULATORS
MAIN
PROGRAMMING
POWER
AUXILIARY HARDWARE
PINOUT
SUPPORTING IMAGES
LEDS
ACCELEROMETER

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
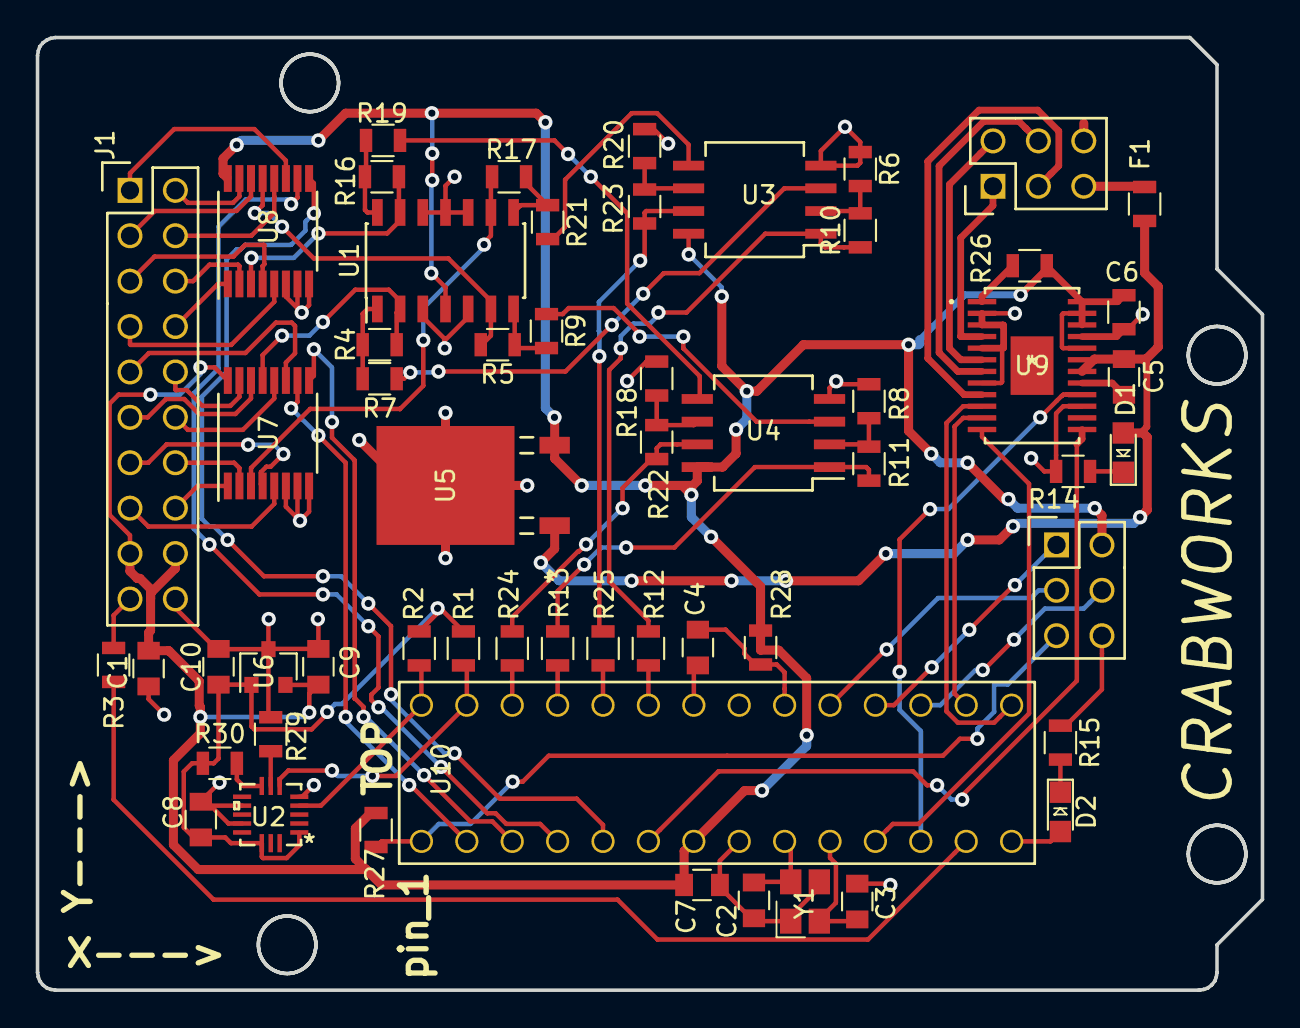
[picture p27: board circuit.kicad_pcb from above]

Board: 2 copper layers, 68.5 x 53.3 mm, 57 parts (0 on the bottom side), 76 nets.

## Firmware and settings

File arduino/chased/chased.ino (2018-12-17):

#include <Adafruit_NeoPixel.h>
#include <Wire.h>
#include <Adafruit_LIS3DH.h>
#include <Adafruit_Sensor.h>
#include "WS2812_Definitions.h"

// -----------------------
// DEFINE PINS
// -----------------------
#define RED A2 // input for red photodiode
#define BLUE A3 // input for blue photodiode

#define BPWM 10
#define APWM 9
#define BDIR 5
#define ADIR 4

#define MUX0 2
#define MUX1 3

#define LED_COUNT 20
#define LED_INPUT 7


// ---------------------
// DEFINE VARIABLES TO 
// READ SENSORS
// ---------------------

// front = 0, right = 1, left = 2, back = 3 
int init_red_front; // ambient reference value
int init_red_right;
int init_red_left;
int init_red_back;
int init_blue_front;
int init_blue_right;
int init_blue_left;
int init_blue_back;

int curr_red_front; // current value 
int curr_red_right;
int curr_red_left;
int curr_red_back;
int curr_blue_front;
int curr_blue_right;
int curr_blue_left;
int curr_blue_back;

int diff_red_front; // difference between ambient and current value
int diff_red_right;
int diff_red_left;
int diff_red_back;
int diff_blue_front;
int diff_blue_right;
int diff_blue_left;
int diff_blue_back;

int left2red;
int right2red;
int left2blue;
int right2blue;

int left3red;
int right3red;
int left3blue;
int right3blue;

int mux_delay = 5;
int motor_delay = 5;

unsigned long prevTime = 0;
unsigned long currTime;
int programCounter = 0;

bool bump = false;

// ---------------------
// DEFINE VARIABLES TO 
// SEND MOTOR COMMANDS
// ---------------------
float left1; // left motor commands to be summed 
float left2;
float left3;
float left4;

float right1; // right motor commands to be summed
float right2;
float right3;
float right4;

float left_total = 0;
float right_total = 0;

float sens = 2;
float scale = 1;
int bluesum;

// ---------------------
// DEFINE VARIABLES FOR
// LED STRIP
// ---------------------

int brightness = 64;
int R = 20;
int G = 0;
int B = 0;
Adafruit_NeoPixel strip = Adafruit_NeoPixel(LED_COUNT, LED_INPUT, NEO_RGB + NEO_KHZ800);

Adafruit_LIS3DH lis = Adafruit_LIS3DH();

void setup() {
  delay(5000);
  Serial.begin(9600);
  
  pinMode(RED,INPUT);
  pinMode(BLUE,INPUT);

  pinMode(APWM,OUTPUT);
  pinMode(ADIR,OUTPUT);

  pinMode(BPWM,OUTPUT);
  pinMode(BDIR,OUTPUT);
 
  pinMode(MUX0, OUTPUT);
  pinMode(MUX1, OUTPUT);

  pinMode(LED_INPUT, OUTPUT);

  digitalWrite(MUX0, HIGH); // set mux select to 0
  digitalWrite(MUX1, HIGH);
  delay(150);
  init_red_front = analogRead(RED); // take initial front values to calibrate
  init_blue_front = analogRead(BLUE);

  digitalWrite(MUX0, HIGH); // set mux select to 1
  digitalWrite(MUX1, LOW);
  delay(150);
  init_red_right = analogRead(RED); // take initial right values to calibrate
  init_blue_right = analogRead(BLUE);

  digitalWrite(MUX0, LOW); // set mux select to 2
  digitalWrite(MUX1, HIGH);
  delay(150);
  init_red_left = analogRead(RED); // take initial left values to calibrate
  init_blue_left = analogRead(BLUE);

  digitalWrite(MUX0, LOW); // set mux select to 3
  digitalWrite(MUX1, LOW);
  delay(150);
  init_red_back = analogRead(RED); // take initial back values to calibrate
  init_blue_back = analogRead(BLUE);

  if (! lis.begin(0x18)) {   // change this to 0x19 for alternative i2c address
    while (1){
      digitalWrite(8,HIGH);
      delay(250);
      digitalWrite(8,LOW);
      delay(250);
    }
  }
  lis.setRange(LIS3DH_RANGE_16_G);   // 2, 4, 8 or 16 G!

  strip.begin(); 
  colorWipe(strip.Color(0, 0, 0)); // Off   
  strip.show(); 
}

void loop() {
  
  currTime = millis();
  
  //ReadPhotodiodes();
  lis.read();      // get X Y and Z data at once
  sensors_event_t event; 
  lis.getEvent(&event);

  bluesum = diff_blue_front + diff_blue_right + diff_blue_left + diff_blue_back;
  if(abs(event.acceleration.z) > 10) {
    if (bump){
      bump = false;
    }
    else if(!bump && bluesum >= 7) {
      bump = true;
    }
  }

  if(bump) {
    colorWipe(strip.Color(0, 0, 0)); // Off
    analogWrite(APWM,0);
    analogWrite(BPWM,0);
    
  } else {
    colorWipe(strip.Color(0, 255, 0)); // Red
    ReadPhotodiodes();
    Move();

  }

  //Move();
}


int ReadPhotodiodes() {
  // ---------------------------
//  find current values of red
//  and blue by subtracting from
//  ambient value
//
//  take reading from front
//  r -> +L +R
//  b -> 0
//  scale values based on brightness 
// ----------------------------
   
  digitalWrite(MUX0, HIGH); // set mux select to 0
  digitalWrite(MUX1, HIGH);
  delay(mux_delay);
  //curr_red_front = analogRead(RED);
  curr_blue_front = analogRead(BLUE);

  //diff_red_front = curr_red_front - init_red_front;
  diff_blue_front = curr_blue_front - init_blue_front; // act based on difference from ambient value

  // left1 = sens*diff_red_front; // scaled motor values from front sensors
  // right1 = sens*diff_red_front;

  /*if(diff_red_front >= 10) {
    left1 = 100;
    right1 = 100;
  } else {
    left1 = 0;
    right1 = 0;
  }*/

// ---------------------------
//  take reading from right
//  r -> +L -R
//  b -> -L +R
// ----------------------------

  digitalWrite(MUX0, HIGH); // set mux select to 1
  digitalWrite(MUX1, LOW);
  delay(mux_delay);
  curr_red_right = analogRead(RED);
  curr_blue_right = analogRead(BLUE);

  diff_red_right = curr_red_right - init_red_right;
  diff_blue_right = curr_blue_right - init_blue_right;

  if(diff_red_right >= 5) {
    left2red = 10 + (sens*diff_red_right);
    right2red = 10 + (sens*diff_red_right);
  } else {
    left2red = 0;
    right2red = 0;
  }

  if(diff_blue_right >= 5) {
    left2blue = 50 + (sens*diff_blue_right);
    right2blue = 50 + (sens*diff_blue_right);
  } else {
    left2blue = 0;
    right2blue = 0;
  }

  left2 =  left2red -
  left2blue;
  //left2 = -left2blue;
  right2 = -right2red + right2blue;
  //right2 = right2blue;

  // left2 = (sens*diff_red_right) - (sens*diff_blue_right);
  // right2 = -(sens*diff_red_right) + (sens*diff_blue_right);

// ---------------------------
//  take reading from left
//  r -> -L +R
//  b -> +L -R
// ----------------------------

  digitalWrite(MUX0, LOW); // set mux select to 2
  digitalWrite(MUX1, HIGH);
  delay(mux_delay);
  curr_red_left = analogRead(RED);
  curr_blue_left = analogRead(BLUE);

  diff_red_left = curr_red_left - init_red_left;
  diff_blue_left = curr_blue_left - init_blue_left;

  if(diff_red_left >= 5) {
    left3red = 10 + (sens*diff_red_left);
    right3red = 10 + (sens*diff_red_left);
  } else {
    left3red = 0;
    right3red = 0;
  }

  if(diff_blue_left >= 5) {
    left3blue = 50 + (sens*diff_blue_left);
    right3blue = 50 + (sens*diff_blue_left);
  } else {
    left3blue = 0;
    right3blue = 0;
  }

  left3 = -left3red + left3blue;
  //left3 = left3blue;
  right3 = right3red - right3blue;
  //right3 = -right3blue;

  // ---------------------------
//  take reading from back
//  r -> 0
//  b -> +L +R
// ----------------------------

  digitalWrite(MUX0, LOW); // set mux select to 3
  digitalWrite(MUX1, LOW);
  delay(mux_delay);
  //curr_red_back = analogRead(RED);
  curr_blue_back = analogRead(BLUE);
  right_total = scale*(right1 + right2 + right3 + right4);

  //diff_red_back = curr_red_back - init_red_back;
  diff_blue_back = curr_blue_back - init_blue_back;

  // left4 = (sens*diff_red_back) + (sens*diff_blue_back);
  // right4 = 0;

  if(diff_blue_back >= 10) {
    left1 = 100;
    right1 = 100;
  } else {
    left1 = 0;
    right1 = 0;
  }
}

int Move() {
  // ----------------------------
  // Sum all motor response and 
  // send response to the motors
  // ----------------------------

   left_total = scale*(left1 + left2 + left3 + left4) - 40;
   right_total = scale*(right1 + right2 + right3 + right4) - 40;

   digitalWrite(ADIR,HIGH);
   digitalWrite(BDIR,LOW);

   /*if(diff_red_front >= 80) {
    left_total = 0;
    right_total = 0;
   }*/

   if(left_total <= 0) {
    left_total = 0;
   }
   if(right_total <= 0) {
    right_total = 0;
   }

   analogWrite(APWM,left_total);
   analogWrite(BPWM,right_total);
   delay(motor_delay);
}

void colorWipe(uint32_t c) {
  for(uint16_t i=0; i<strip.numPixels(); i++) {
    strip.setPixelColor(i, c);
    strip.show();
  }
}

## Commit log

2018-10-21 added new code for reading sensor values that could have changing frequencies
2018-10-21 added a schematic for our circuit
    [circuit.kicad_pcb, circuit.sch]
2018-10-31 made progress on schematic
    [circuit.sch]
2018-11-04 more progess git add -A!
    [circuit.sch]
2018-11-04 finished schematic for main board
    [circuit.sch]
2018-11-05 started on layout. *make crab noise*
    [circuit.kicad_pcb, circuit.sch]
2018-11-06 finished board
    [circuit.kicad_pcb, circuit.sch]
2018-11-06 Adding beacon schematic
    [beacon-B.Cu.gbr, beacon-B.Mask.gbr, beacon-B.Paste.gbr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]
2018-11-06 generated gerber files
    [circuit-B.Cu.gbr, circuit-B.Mask.gbr, circuit-B.SilkS.gbr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]
2018-11-06 Adding gerber files
2018-11-07 added pictures of the pcb
2018-11-25 added pics of layout for pcb
2018-11-25 added arduino code
2018-11-30 diodetest is to set mux and test photodiodes/motors
2018-12-12 updated arduino code. vectorizedmotion is most recent motion code
2018-12-13 CAD files
    [18650.SLDPRT, 2_cell_holder_18650_v5.SLDPRT, Assem_v5.SLDASM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]
2018-12-14 Added a LED circuit
    [beacon-B.Cu.gbr, beacon-B.Mask.gbr, beacon-B.Paste.gbr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]
2018-12-14 Added a new LED circuit
    [circuit.sch]
2018-12-14 added a pdf of our schematic

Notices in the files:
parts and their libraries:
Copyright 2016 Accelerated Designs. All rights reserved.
